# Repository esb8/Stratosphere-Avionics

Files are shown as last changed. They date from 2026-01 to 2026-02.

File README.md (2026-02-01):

# Stratosphere
Stratosphere is a highly **versatile** avionics stack designed for a variety of **Remote-Controlled** (RC) vehicles such as planes, model rockets, and drones. Stratosphere is designed for *verstaility*, allowing for usage as a standalone stack and alongside off the shelf modules (VTX, GPS, etc), servos and ESCs. 

## Features
- **Flight Computer**
  - 6-axis IMU (ICM-42605)
  - High Precision Barometer (BMP388)
  - 915MHz LoRa Transciever (ELRS compatible)
  - 4 UART Outputs
  - 8 PWM capable pins
  - 4 PWM/Motor control pins (4-in-1 ESC compatible) 
  - STM32F405
  - USB-C programming
- **Power Management Unit**
  - 2-4S LiPo (7.4V-14.8V)
  - 3.3V 3A (3+ outputs)
  - 5V 3A (3+ outputs)
  - Compact + Affordable
  - XT60

## Media

**Power Management Board**


## Future Deliveries
- Update PMU connector amount (5V 3 pin to 5 pin) (4 servos + VTX).
- Power ORING/multiplexer circuit on FC.
- Layout FC
- Current Calcs

## License

This project is released under the MIT License. All design files, including schematics, PCB layouts, and firmware are open source and available for personal and commercial use with attribution.

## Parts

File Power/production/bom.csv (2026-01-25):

Designator | Footprint | Quantity | Value | LCSC Part #
C1, C2, C21 | C_0805 | 3 | 22uF | C45783
C10, C11 | C_0805 | 2 | 47uF | C16780
C13, C14 | C_0402 | 2 | 10nF | C15195
C15, C18, C7, C9 | C_0402 | 4 | 100nF | C1525
C17 | C_0402 | 1 | 4.7nF | C1538
C19 | C_0402 | 1 | 33pF | C1562
C4, C5 | C_0603 | 2 | 10uF | C96446
C6 | C_0402 | 1 | 1nF | C1523
C8 | C_0402 | 1 | 47pF | C1567
D1, D2 | D_SMA | 2 | SS32
D3 | D_0603 | 1 | Red | C2286
D4 | D_0603 | 1 | White | C2290
D6 | D_0603 | 1 | Yellow | C89811
J1 | JST_GH_SM04B-GHS-TB_1x04-1MP_P1.25mm_Horizontal | 1 | Conn_01x04_Pin
J2 | AMASS_XT30UPB-M_1x02_P5.0mm_Vertical | 1 | Conn_01x02
J3 | JST_GH_SM06B-GHS-TB_1x06-1MP_P1.25mm_Horizontal | 1 | Conn_01x06
J5 | TestPoint_Pad_2.0x2.0mm | 1 | GND
J6 | TestPoint_Pad_2.0x2.0mm | 1 | +BATT
Q2, Q3, Q4 | Q_SOT-23 | 3 | AO3400A | C20917
R1 | R_0402 | 1 | 27kΩ | C25771
R10, R11, R14, R5, R9 | R_0402 | 5 | 10kΩ | C25744
R12 | R_0603 | 1 | 1.8kΩ | C4177
R13 | R_0402 | 1 | 200Ω | C25087
R15 | R_0603 | 1 | 430Ω | C23170
R16 | R_0603 | 1 | 820Ω | C23253
R18 | R_0402 | 1 | 49.9kΩ | C25897
R2, R7 | R_0402 | 2 | 330kΩ | C25778
R3 | R_0402 | 1 | 2kΩ | C4109
R4, R8 | R_0402 | 2 | 100kΩ | C25741
R6 | R_0402 | 1 | 3.3kΩ | C25890
TP1, TP2, TP3, TP4, TP5, TP6 | TestPoint_Pad_1.5x1.5mm | 6 | TestPoint
U1, U3 | SOIC-8_L5.0-W4.0-P1.27-LS6.0-BL | 2 | TPS54331DR | C9865
U2, U4 | IND-SMD_L4.0-W4.0_XAL4030-682MEC | 2 | XAL4030-682MEC | C3040663

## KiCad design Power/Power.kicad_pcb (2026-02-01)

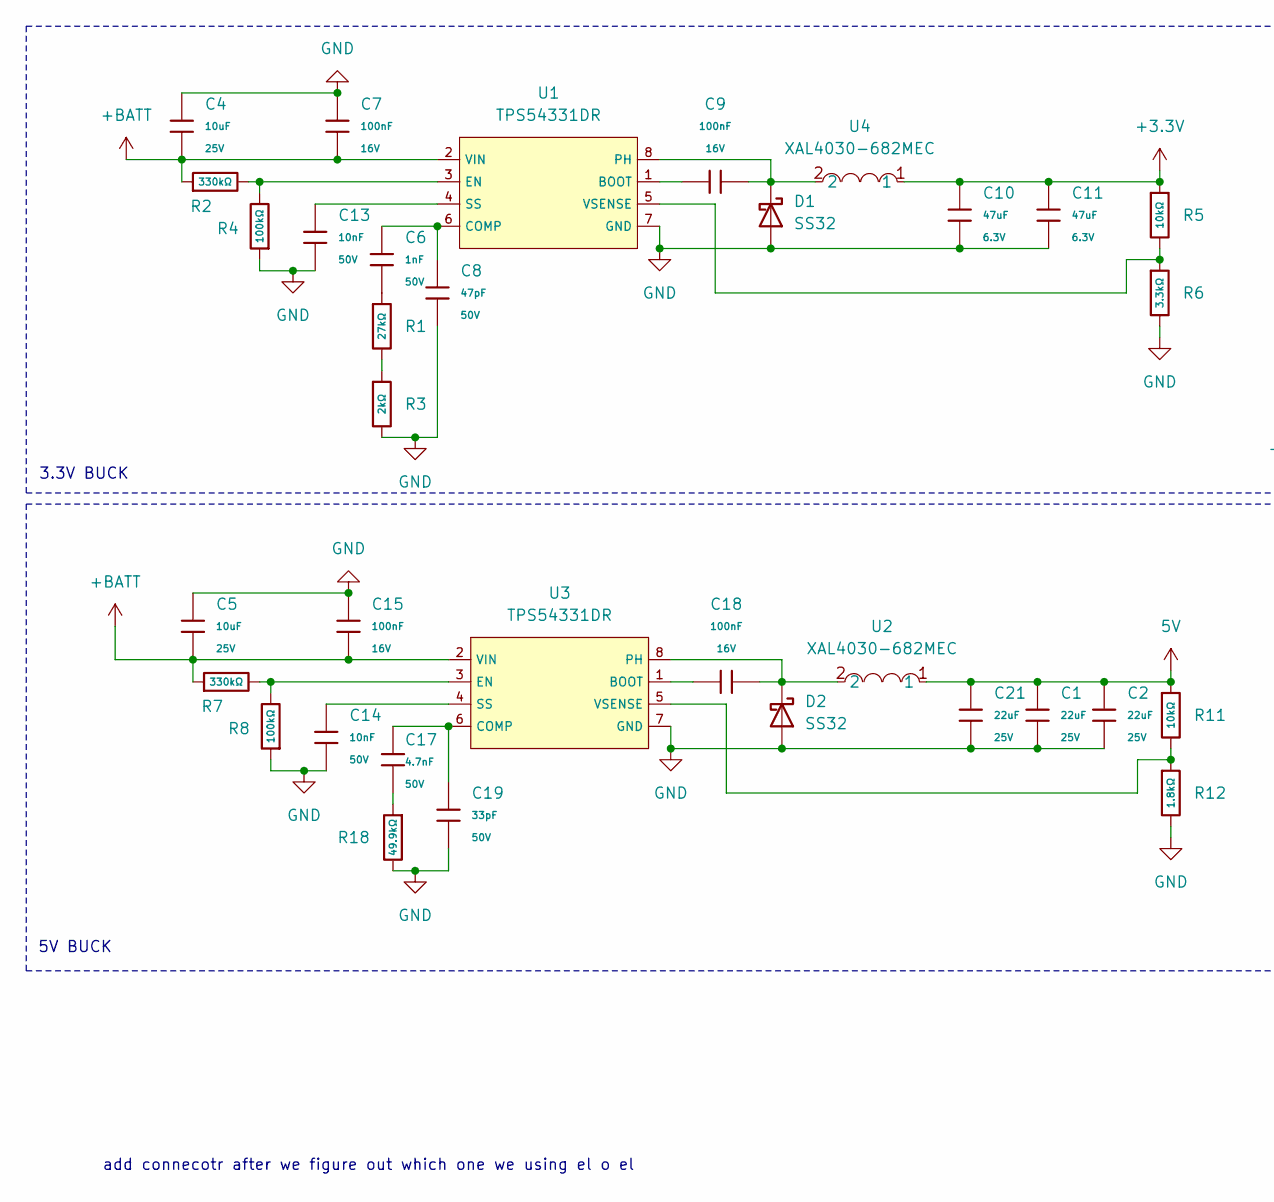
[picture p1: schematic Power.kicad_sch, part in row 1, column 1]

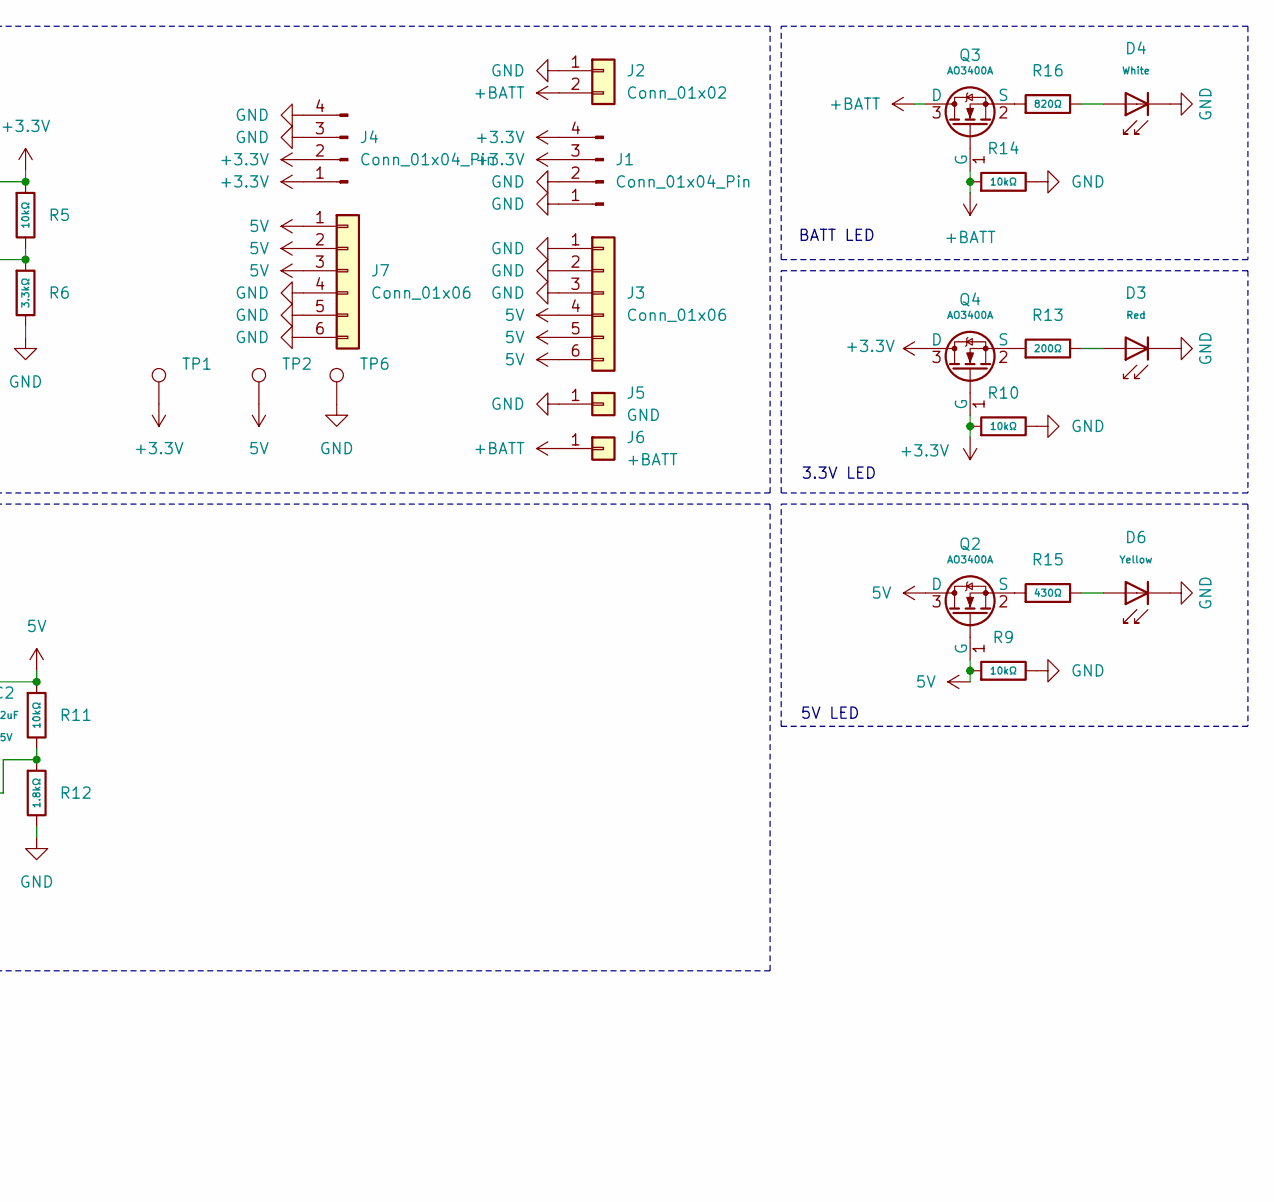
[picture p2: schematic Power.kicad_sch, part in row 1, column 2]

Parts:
C1, C2, C21: 22uF; C_0805; Voltage Rated 25V; Tolerance ±20%; Part CL21A226MAQNNNE; LCSC C45783
C4, C5: 10uF; C_0603; Voltage Rated 25V; Tolerance ±20%; Part CL10A106MA8NRNC; LCSC C96446
C6: 1nF; C_0402; Voltage Rated 50V; Tolerance ±10%; Part 0402B102K500NT; LCSC C1523
C7, C9, C15, C18: 100nF; C_0402; Voltage Rated 16V; Tolerance ±10%; Part CL05B104KO5NNNC; LCSC C1525
C8: 47pF; C_0402; Voltage Rated 50V; Tolerance ±5%; Part 0402CG470J500NT; LCSC C1567
C10, C11: 47uF; C_0805; Voltage Rated 6.3V; Tolerance ±20%; Part CL21A476MQYNNNE; LCSC C16780
C13, C14: 10nF; C_0402; Voltage Rated 50V; Tolerance ±10%; Part CL05B103KB5NNNC; LCSC C15195
C17: 4.7nF; C_0402; Voltage Rated 50V; Tolerance ±10%; Part 0402B472K500NT; LCSC C1538
C19: 33pF; C_0402; Voltage Rated 50V; Tolerance ±5%; Part 0402CG330J500NT; LCSC C1562
D1, D2: SS32; D_SMA
D3: Red; D_0603; Part KT-0603R; LCSC C2286
D4: White; D_0603; Part KT-0603W; LCSC C2290
D6: Yellow; D_0603; Forward Voltage (VF) 1.6V~2.6V; Part NCD0603Y2; LCSC C89811
J1, J4: Conn_01x04_Pin; JST_GH_SM04B-GHS-TB_1x04-1MP_P1.25mm_Horizontal
J2: Conn_01x02; AMASS_XT30UPB-M_1x02_P5.0mm_Vertical
J3, J7: Conn_01x06; JST_GH_SM06B-GHS-TB_1x06-1MP_P1.25mm_Horizontal
J5: GND; TestPoint_Pad_2.5x2.5mm
J6: +BATT; TestPoint_Pad_2.5x2.5mm
Q2, Q3, Q4: AO3400A; Q_SOT-23; Part AO3400A; LCSC C20917
R1: 27kΩ; R_0402; Overload Voltage (Max) 50V; Tolerance ±1%; Part 0402WGF2702TCE; LCSC C25771
R2, R7: 330kΩ; R_0402; Overload Voltage (Max) 50V; Tolerance ±1%; Part 0402WGF3303TCE; LCSC C25778
R3: 2kΩ; R_0402; Overload Voltage (Max) 50V; Tolerance ±1%; Part 0402WGF2001TCE; LCSC C4109
R4, R8: 100kΩ; R_0402; Overload Voltage (Max) 50V; Tolerance ±1%; Part 0402WGF1003TCE; LCSC C25741
R5, R9, R10, R11, R14: 10kΩ; R_0402; Overload Voltage (Max) 50V; Tolerance ±1%; Part 0402WGF1002TCE; LCSC C25744
R6: 3.3kΩ; R_0402; Overload Voltage (Max) 50V; Tolerance ±1%; Part 0402WGF3301TCE; LCSC C25890
R12: 1.8kΩ; R_0603; Overload Voltage (Max) 75V; Tolerance ±1%; Part 0603WAF1801T5E; LCSC C4177
R13: 200Ω; R_0402; Overload Voltage (Max) 50V; Tolerance ±1%; Part 0402WGF2000TCE; LCSC C25087
R15: 430Ω; R_0603; Overload Voltage (Max) 75V; Tolerance ±1%; Part 0603WAF4300T5E; LCSC C23170
R16: 820Ω; R_0603; Overload Voltage (Max) 75V; Tolerance ±1%; Part 0603WAF8200T5E; LCSC C23253
R18: 49.9kΩ; R_0402; Overload Voltage (Max) 50V; Tolerance ±1%; Part 0402WGF4992TCE; LCSC C25897
TP1, TP2, TP6: TestPoint; TestPoint_Pad_2.0x2.0mm
U1, U3: TPS54331DR; SOIC-8_L5.0-W4.0-P1.27-LS6.0-BL; Output Voltage 0.8V~25V; Input Voltage 3.5V~28V; Part TPS54331DR; LCSC C9865
U2, U4: XAL4030-682MEC; IND-SMD_L4.0-W4.0_XAL4030-682MEC; LCSC Part C3040663

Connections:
5V: C1.1, C2.1, C21.1, J3.4, J3.5, J3.6, J7.1, J7.2, J7.3, Q2.1 (G), Q2.3 (D), R9.1, R11.1, TP2.1, U2.1
+3.3V: C10.1, C11.1, J1.3, J1.4, J4.1, J4.2, Q4.1 (G), Q4.3 (D), R5.1, R10.1, TP1.1, U4.1
+BATT: C4.1, C5.1, C7.2, C15.2, J2.2, J6.1, Q3.1 (G), Q3.3 (D), R2.1, R7.1, R14.1, U1.2 (VIN), U3.2 (VIN)
GND: C1.2, C2.2, C4.2, C5.2, C7.1, C8.2, C10.2, C11.2, C13.2, C14.2, C15.1, C19.2, C21.2, D1.2 (A), D2.2 (A), D3.1, D4.1, D6.1, J1.1, J1.2, J2.1, J3.1, J3.2, J3.3, J4.3, J4.4, J5.1, J7.4, J7.5, J7.6, R3.2, R4.1, R6.2, R8.1, R9.2, R10.2, R12.2, R14.2, R18.2, TP6.1, U1.7 (GND), U3.7 (GND)
unnamed: C6.2, R1.1
unnamed: C17.2, R18.1
unnamed: C9.2, D1.1 (K), U1.8 (PH), U4.2
unnamed: C18.2, D2.1 (K), U2.2, U3.8 (PH)
unnamed: D3.2, R13.2
unnamed: D4.2, R16.2
unnamed: D6.2, R15.2
unnamed: Q2.2 (S), R15.1
unnamed: Q3.2 (S), R16.1
unnamed: Q4.2 (S), R13.1
unnamed: R1.2, R3.1
unnamed: C9.1, U1.1 (BOOT)
unnamed: C6.1, C8.1, U1.6 (COMP)
unnamed: R2.2, R4.2, U1.3 (EN)
unnamed: C13.1, U1.4 (SS)
unnamed: R5.2, R6.1, U1.5 (VSENSE)
unnamed: C18.1, U3.1 (BOOT)
unnamed: C17.1, C19.1, U3.6 (COMP)
unnamed: R7.2, R8.2, U3.3 (EN)
unnamed: C14.1, U3.4 (SS)
unnamed: R11.2, R12.1, U3.5 (VSENSE)

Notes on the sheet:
BATT LED
5V LED
3.3V BUCK
add connecotr after we figure out which one we using el o el
5V BUCK
3.3V LED

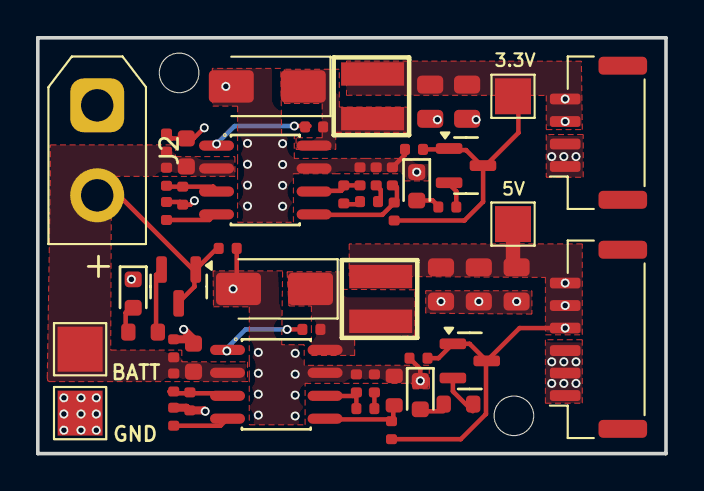
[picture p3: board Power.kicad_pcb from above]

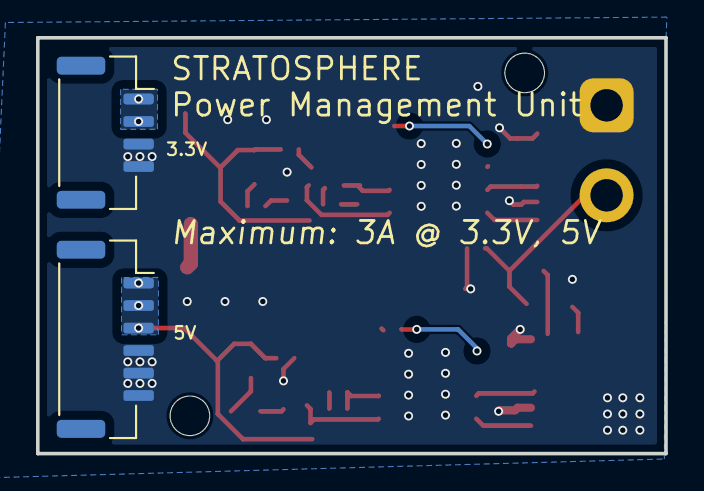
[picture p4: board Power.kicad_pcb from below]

Board: 2 copper layers, 34.9 x 23.1 mm, 55 parts (2 on the bottom side), 25 nets.

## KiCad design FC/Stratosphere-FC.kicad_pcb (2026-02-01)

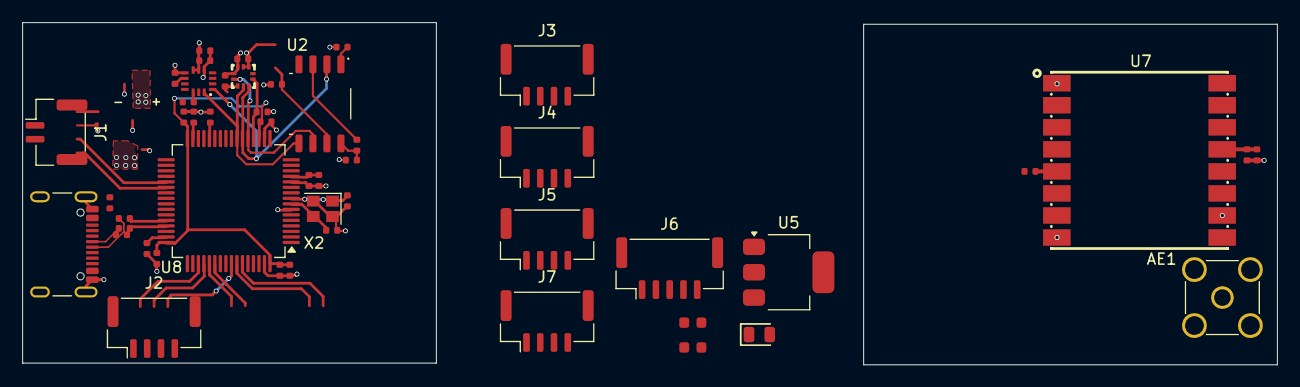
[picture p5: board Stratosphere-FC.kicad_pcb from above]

Board: 2 copper layers, 113.9 x 31.1 mm, 49 parts (0 on the bottom side), 35 nets.

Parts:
AE1: 915MHZ Antenna; SMA_Amphenol_901-144_Vertical
C1, C2, C6, C12, C16, C17, C19, C22, C23, C28: 100nF; C_0402
C3: 10uF; C_0402
C4, C5: 22uF; C_0603
C7, C13, C14: 2.2uF; C_0402
C8: 10nF; C_0402
C24: 4.7uF; C_0402
C30: 1uF; C_0402
C32, C33: 20pF; C_0402
D3: Green; D_0805
J1: Connector; JST_GH_BM02B-GHS-TBT_1x02-1MP_P1.25mm_Vertical
J2, J3, J4, J5, J7: Conn_01x04; JST_GH_BM04B-GHS-TBT_1x04-1MP_P1.25mm_Vertical
J6: Conn_01x05; JST_GH_BM05B-GHS-TBT_1x05-1MP_P1.25mm_Vertical
P2: USB_C_Plug_USB2.0; USB_C_Receptacle_GCT_USB4105-xx-A_16P_TopMnt_Horizontal
R1, R3, R4, R7, R10, R12, R15, R17: 5.1kΩ; R_0402
R9, R16: 22Ω; R_0402
R11: 200Ω; R_0402
U1: ICM-42605; LGA-14_L3.0-W2.5-P0.50-TL
U2: W25Q16JVSS; SOIC-8_5.3x5.3mm_P1.27mm
U3: BMP388; SENSORM-SMD_BMP388
U5: AMS1117; SOT-223-3_TabPin2
U7: 915MHz; COMM-SMD_LORA1276-C1-915MHZ
U8: STM32F405RGTx; LQFP-64_10x10mm_P0.5mm
X2: Shenzhen SCTF Elec SX2B12.000F1010F30; Crystal_SMD_2520-4Pin_2.5x2.0mm

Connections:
+3.3V: C1.2, C2.1, C3.1, C4.1, C6.2, C7.1, C8.2, C12.1, C28.1, J1.1, J3.3, J4.3, J5.3, J6.4, R3.2, R4.2, R7.2, R10.1, R11.1, R12.1, R15.1, U1.5 (VDDIO), U1.8 (VDD), U2.8 (VCC), U3.1 (VDDIO), U3.10 (VDD), U5.2 (VO), U7.13 (VCC)
+5V: C5.1, P2.A4 (VBUS), P2.A9 (VBUS), P2.B4 (VBUS), P2.B9 (VBUS), U5.3 (VI)
/BOOT1: R17.1, U8.28 (PB2)
/OSC_IN: C32.1, U8.6 (PH1), U8.8 (PC0), X2.3 (OSC)
/OSC_OUT: C33.2, U8.5 (PH0), U8.9 (PC1), X2.1 (OSC)
/SPI1_MISO: U1.1 (AP_SDO/AP_AD0), U2.2 (DO/IO_{1}), U3.5 (SDO), U8.22 (PA6)
/SPI1_MOSI: U1.14 (AP_SDA/AP_SDIO/AP_SDI), U2.5 (DI/IO_{0}), U3.4 (SDI), U8.23 (PA7)
/SPI1_NSS: R15.2, U3.6 (CSB), U8.20 (PA4)
/SPI1_SCK: U1.13 (AP_SCL/AP_SCLK), U2.6 (CLK), U3.2 (SCK), U8.21 (PA5)
/SPI2_NSS: R12.2, U1.12 (AP_CS)
/SPI3_MISO: J6.2, U7.2 (MISO), U8.52 (PC11)
/SPI3_MOSI: J6.3, U7.3 (MOSI), U8.57 (PB5)
/SPI3_NSS: R10.2, U7.5 (NSS)
/SPI3_SCK: J6.1, U7.4 (SCK), U8.51 (PC10)
/SPI5_NSS: R7.1, U2.1 (~CS)
/UART5_RX: J5.1, U8.53 (PC12)
/UART5_TX: J5.2, U8.54 (PD2)
/USART1_RX: J4.2, U8.59 (PB7)
/USART1_TX: J4.1, U8.58 (PB6)
/USART6_RX: J3.2, U8.38 (PC7)
/USART6_TX: J3.1, U8.37 (PC6)
/USB_FS_DN: P2.A7 (D-), R16.2
/USB_FS_DP: P2.A6 (D+), R9.2
GND: C1.1, C2.2, C3.2, C4.2, C5.2, C6.1, C7.2, C8.1, C12.2, C13.2, C14.2, C16.2, C17.2, C19.2, C22.2, C23.2, C24.2, C28.2, C30.2, C32.2, C33.1, D3.1, J1.2, J3.4, J4.4, J5.4, J6.5, P2.A1 (GND), P2.A12 (GND), P2.B1 (GND), P2.B12 (GND), P2.S1 (SHIELD), R1.1, R17.2, U1.6 (GND), U1.7 (RESV), U1.9 (INT2/FSYNC), U2.4 (GND), U3.3 (VSS), U3.8 (VSS), U3.9 (VSS), U5.1 (ADJ), U7.1 (GND), U7.8 (GND), U7.10 (GND), U8.12 (VSSA), U8.18 (VSS), U8.63 (VSS), X2.2 (GND), X2.4 (GND)
unnamed: AE1.1 (A), U7.9 (ANT)
unnamed: C16.1, C17.1, C19.1, C22.1, C24.1, U8.19 (VDD), U8.32 (VDD), U8.48 (VDD), U8.64 (VDD)
unnamed: D3.2, R11.2
unnamed: P2.A5 (CC), R1.2
unnamed: R4.1, U2.7 (~HOLD/~RESET/IO_{3})
unnamed: R3.1, U2.3 (~WP/IO_{2})
unnamed: R16.1, U8.44 (PA11)
unnamed: R9.1, U8.45 (PA12)
unnamed: C13.1, U8.31 (VCAP_1)
unnamed: C14.1, U8.47 (VCAP_2)
unnamed: C23.1, C30.1, U8.13 (VDDA)

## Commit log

2026-01-15 Feat: Initialized Repo with FC schematic and PCB
    [Stratosphere-FC.kicad_pcb, Stratosphere-FC.kicad_sch]
2026-01-25 Feat: Addition of Power Module Schematic PCB
    [Power.kicad_pcb, Power.kicad_sch, Stratosphere-FC.kicad_pcb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]
2026-02-01 fix: updated connector, horzontal to vertical
    [Stratosphere-FC.kicad_pcb, Stratosphere-FC.kicad_sch]
2026-02-01 Completed pin mapping of STM32
    [Stratosphere-FC.kicad_pcb, Stratosphere-FC.kicad_sch]
2026-02-01 feat: Added mounting holes, text and more connectors for PMU
    [Power.kicad_pcb, Power.kicad_sch]
